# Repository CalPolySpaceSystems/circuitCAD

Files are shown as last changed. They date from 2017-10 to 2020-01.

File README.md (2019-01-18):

# Circuit CAD
This repository contains Cal Poly Space Systems' circuit board Design files. 
This includes designed PCBs as well as other resources.
See READMEs in each directory for more information.

# Projects
* UpBoard
* CubeStack
* Flight Recorders
* Peripherals
* Breakouts

# Resources
* Component Libraries
* Design Block/Subassembly Libraries
* CAM jobs for exporting Gerber Files of PCBs

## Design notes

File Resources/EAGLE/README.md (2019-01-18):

# EAGLE Resources
This collection currently contains:
* Parts Libraries
* Design Blocks 
* CAM Jobs
<p>
See each directory's README for more information.

# How to Use These Resources
In order to seamlessly import these resources into your EAGLE environment, follow these steps.

1. Clone this repository to your machine 
2. Open EAGLE. Go to the EAGLE control panel.
3. On the toolbar, select `options->directories`. This controls which directories EAGLE will look for files in. 
4. Add the locations of additional dependencies by placing a semicolon after the default directory followed by the local directory of the dependency.<p>
  
<b>Windows:</b><p>
<a href="https://imgur.com/tBfDsb9">Directory Examples</a>

5. Do this for all resource folders you wish to have access to in EAGLE.
6. Restart EAGLE.

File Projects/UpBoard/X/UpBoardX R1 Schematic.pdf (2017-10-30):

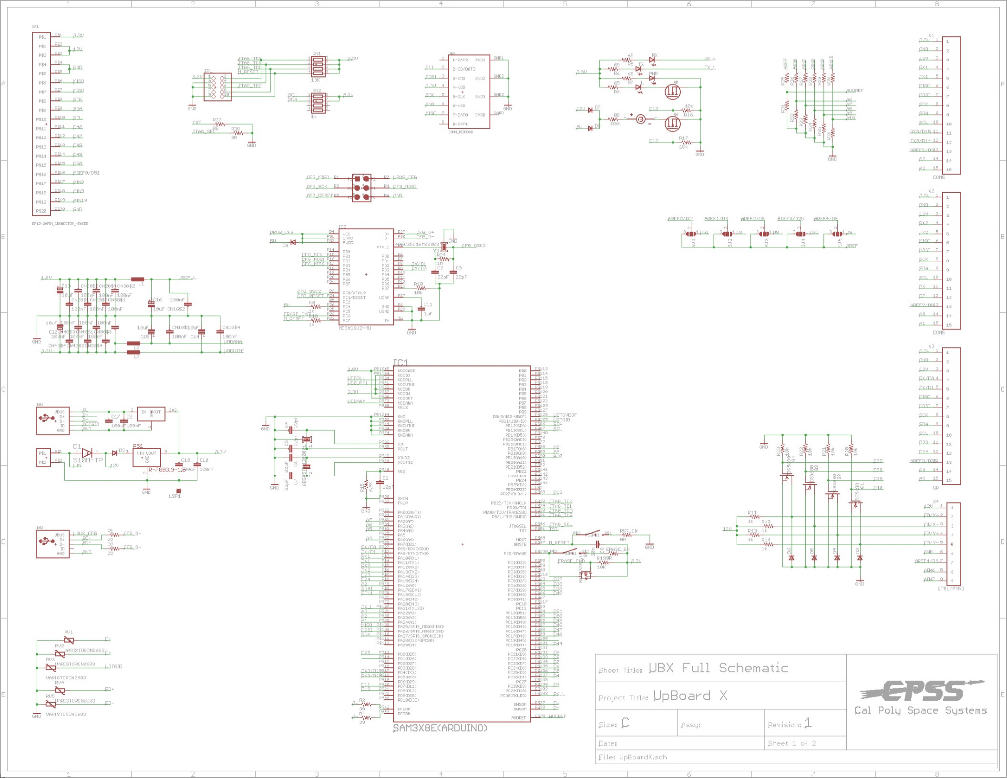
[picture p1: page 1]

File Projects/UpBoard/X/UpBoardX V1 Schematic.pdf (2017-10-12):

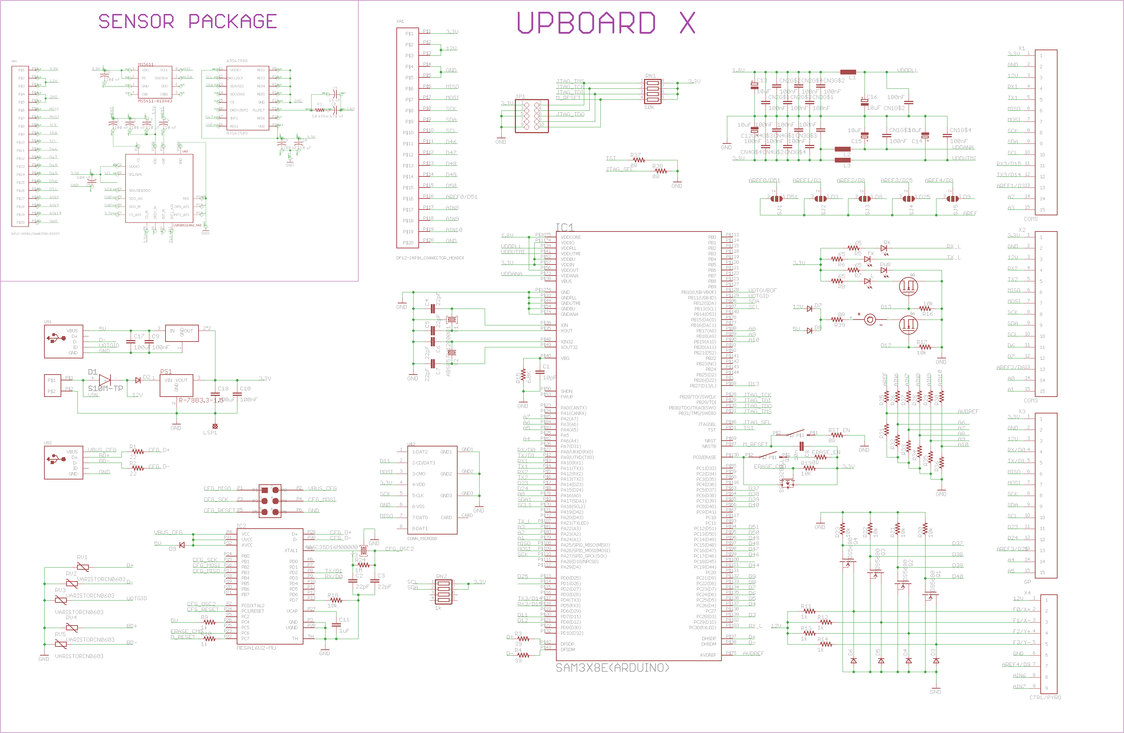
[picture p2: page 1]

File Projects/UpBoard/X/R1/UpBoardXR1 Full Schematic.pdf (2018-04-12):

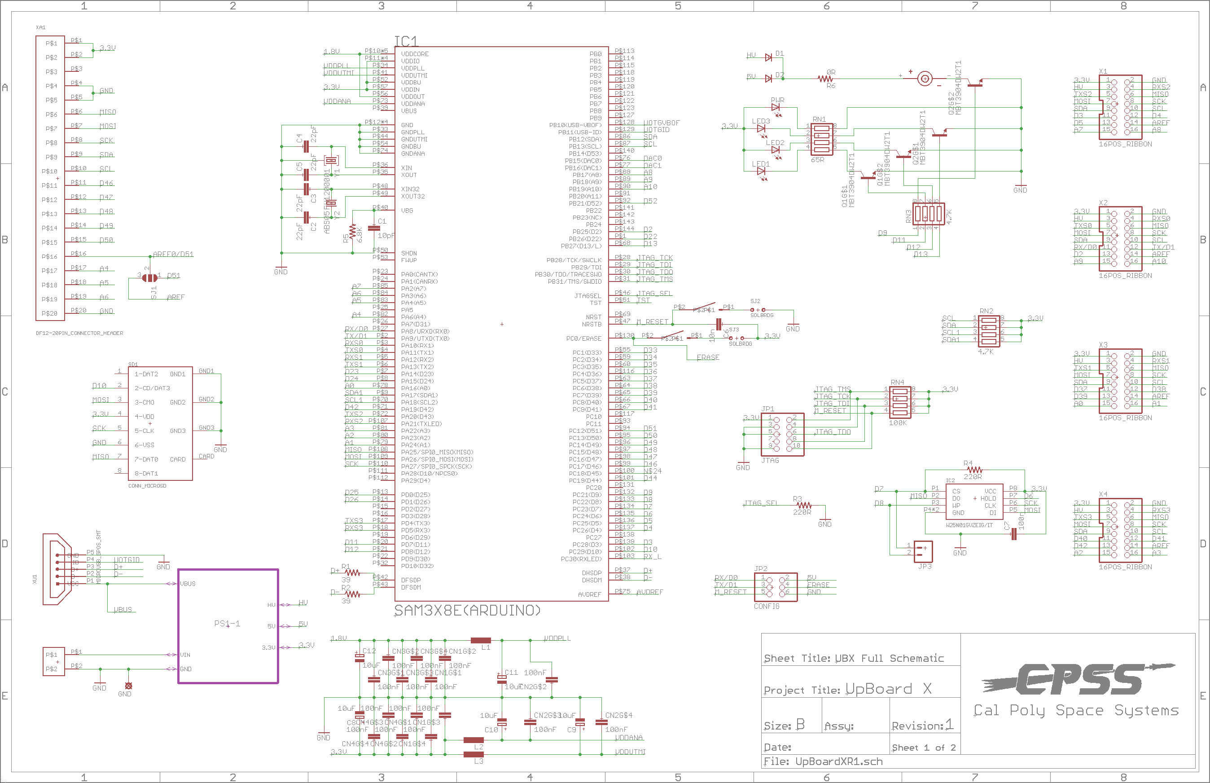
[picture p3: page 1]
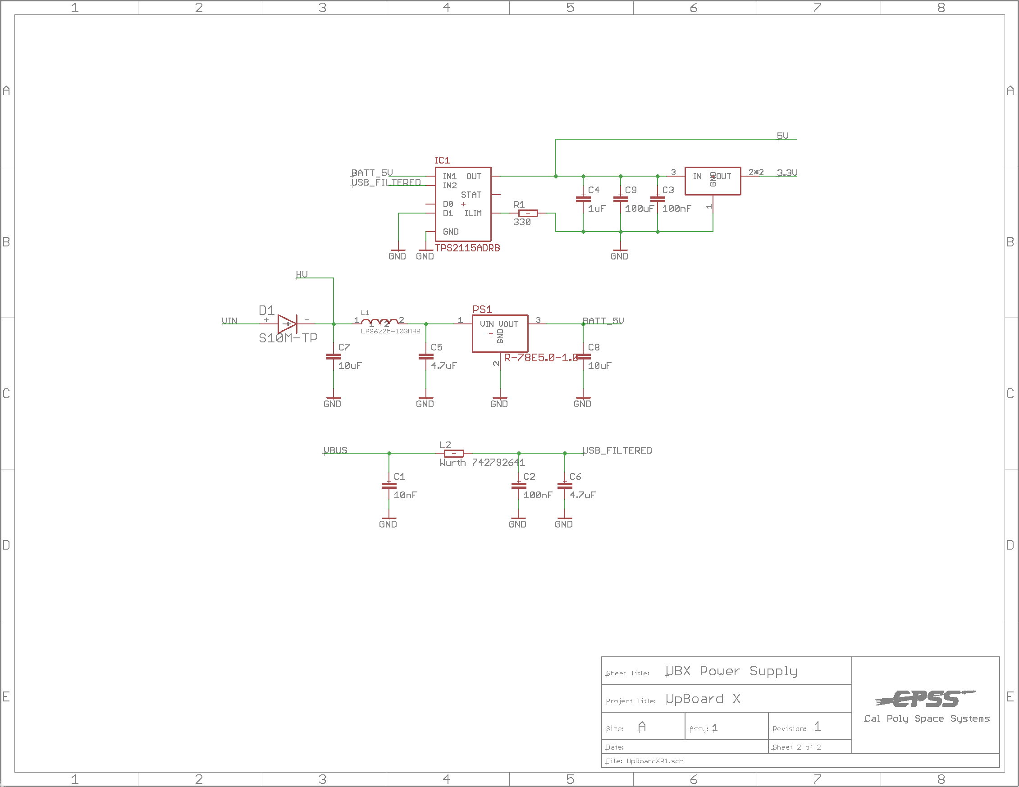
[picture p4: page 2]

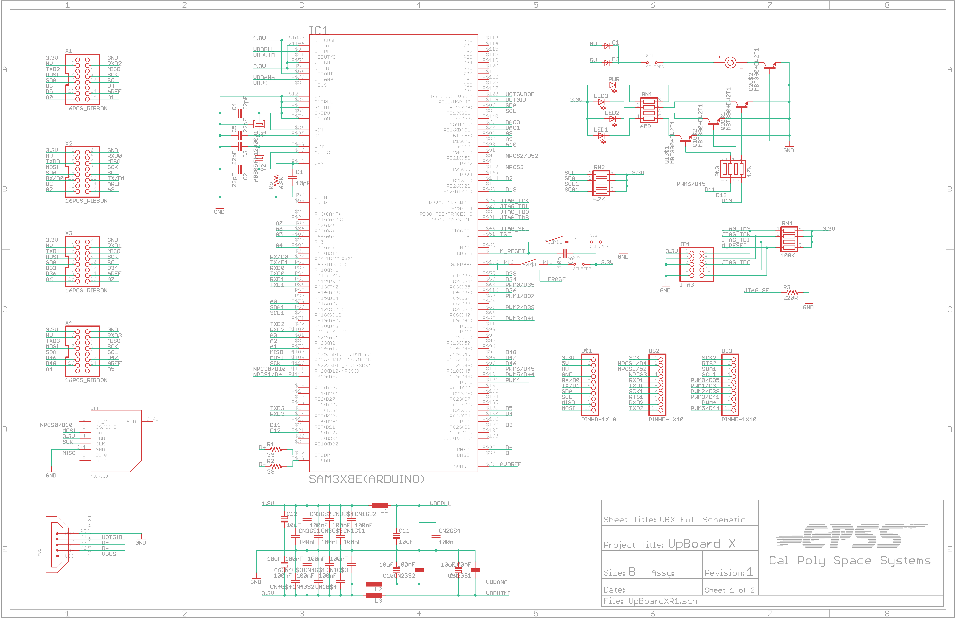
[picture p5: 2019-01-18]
Projects/CubeStack/SAM3X8E Core/cubestack core 1.png

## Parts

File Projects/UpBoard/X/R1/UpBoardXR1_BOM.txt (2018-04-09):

Partlist

Exported from UpBoardXR1.brd at 3/3/2018 10:47 AM

EAGLE Version 8.5.1 Copyright (c) 1988-2017 Autodesk, Inc.

Assembly variant: 

Part      Value                       Package            Library             Position (mil)        Orientation

C1        10pF                        C0603              resistor            (483.62205 1840.47244) R180
C2        22pF                        C0603              resistor            (547.24409 2049.6063) R180
C3        22pF                        C0603              resistor            (547.24409 2246.45669) R180
C4        22pF                        C0603              resistor            (543.54331 2346.37795) R0
C5        22pF                        C0603              resistor            (542.83465 2571.5748) R180
C6        10n                         C0603              resistor            (2356.37795 936.77165) R270
C7        100n                        C0603              resistor            (1800 1990)           R0
C8        10uF                        A/3216-18R         resistor            (1846.45669 1297.24409) R180
C9        10uF                        A/3216-18R         resistor            (1846.45669 1218.50394) R180
C10       10uF                        A/3216-18R         resistor            (1846.45669 1139.76378) R180
C11       10uF                        A/3216-18R         resistor            (1846.45669 1061.02362) R180
C12       10uF                        A/3216-18R         resistor            (1846.45669 982.28346) R180
CN1       100nF                       1206-4             resistor            (1652.75591 1295.27559) R270
CN2       100nF                       1206-4             resistor            (1652.75591 1137.79528) R90
CN3       100nF                       1206-4             resistor            (1652.75591 980.31496) R270
CN4       100nF                       1206-4             resistor            (1497.79528 1134.72441) R180
D1                                    SOD323             zetex               (2932.28346 1692.12598) R0
D2                                    SOD323             zetex               (2931.88976 1841.73228) R0
ERASE     1000P                       B3U-1000P          switch-omron        (2769.84252 1551.33858) R0
GND       LSP10                       LSP10              solpad              (913.30709 1375.11811) R180
IC1       SAM3X8E(ARDUINO)            144-LEAD_LQFP      ATSAM3X             (1100 2031.88976)     R270
IC2       W25N01GVZEIG/IT             WSON               CPSS_IC             (1993.54331 1792.3622) R90
JP1       JTAG                        2X05               pinhead             (2256.61417 2290.55118) R90
JP2       CONFIG                      2X03               pinhead             (2256.61417 1832.28346) R90
JP3                                   1X02               SparkFun-Connectors (1690 1800)           R0
L1                                    C0402              resistor            (1498.89764 1022.83465) R0
L2                                    C0402              resistor            (1496.37795 1262.99213) R0
L3                                    C0402              resistor            (1495.98425 1325.98425) R0
LED1                                  CHIPLED_0805       led                 (1960.62992 2119.68504) R90
LED2                                  CHIPLED_0805       led                 (1963.77953 2253.14961) R90
LED3                                  CHIPLED_0805       led                 (1964.56693 2385.03937) R90
LS1       AI-1440-TWT-24V-2-R         AI-1440-TWT-24-2-R UpBoard             (2718.11024 2124.40945) R180
PS1-1:C1  10nF                        C0603              eagle-ltspice       (1330 1180)           R0
PS1-1:C2  100nF                       C0603              eagle-ltspice       (710 1190)            R90
PS1-1:C3  100nF                       C0603              resistor            (903.77953 1204.96063) R90
PS1-1:C4  1uF                         C0805              eagle-ltspice       (990 1220)            R90
PS1-1:C5  4.7uF                       C1206              eagle-ltspice       (500 1150)            R0
PS1-1:C6  4.7uF                       C0805              eagle-ltspice       (820 1220)            R90
PS1-1:C7  10uF                        C1206              eagle-ltspice       (1277.48031 887.08661) R0
PS1-1:C8  10uF                        C1206              eagle-ltspice       (550 1290)            R0
PS1-1:C9  100uF                       C0805              resistor            (1080 1220)           R90
PS1-1:D1  S10M-TP                     DO-214AB           Power_Utils_Brett   (1274.72441 613.77953) R90
PS1-1:IC1 TPS2115ADRB                 SON-8              Power_Utils_Brett   (933.07087 994.01575) R270
PS1-1:L1  LPS6225-103MRB              INDM600X600X240N   Power_Utils_Brett   (1003.14961 750.31496) R180
PS1-1:L2  Wurth 742792641             R0603              eagle-ltspice       (1190 1180)           R180
PS1-1:PS1 R-78E5.0-1.0                R-78E5.0-1.0       Power_Utils_Brett   (719.68504 829.92126) R90
PS1-1:PS2 AZ1117C                     SOT89              UpBoard B           (1250.23622 1032.51969) R270
PS1-1:R1  330                         R0603              eagle-ltspice       (1015.98425 1090.55118) R0
PWR                                   CHIPLED_0805       led                 (1252.12598 1309.37008) R270
Q1        FFB2222A                    SC-88              CPSS_IC             (1645 2285)           R270
Q2        FFB2222A                    SC-88              CPSS_IC             (1745 2160)           R180
R1        39                          R0603              resistor            (1430 330)            R90
R2        39                          R0603              resistor            (1170 300)            R90
R3        220R                        R0402              resistor            (544.25197 1921.10236) R180
R4        220R                        R0402              resistor            (1710 1920)           R0
R5        6.8K                        R0603              resistor            (551.49606 1748.97638) R0
R6        0R                          R0603              resistor            (2564.96063 1803.93701) R0
RESET     1000P                       B3U-1000P          switch-omron        (2555.43307 1548.8189) R0
RN1       65R                         CTS742C083         resistor-net        (1805 2310)           R90
RN2       4.7K                        CTS742C083         resistor-net        (2056.14173 937.55906) R0
RN3       4.7K                        CTS742C083         resistor-net        (1680 2425)           R270
RN4       100K                        CTS742C083         resistor-net        (2207.95276 937.55906) R0
SD1       CONN_MICROSD                CONN_MICROSD       UpBoard B           (2430.04724 644.93701) R180
SJ1                                   SJ_2               jumper              (2037.40157 1180.31496) R270
SJ2       SOLBRDG                     SOLBRDG            CPSS_CONNECTOR      (2660 1470)           R270
SJ3       SOLBRDG                     SOLBRDG            CPSS_CONNECTOR      (2880 1470)           R270
X1        16POS_RIBBON                2X08               CPSS_CONNECTOR      (3300 890)            R270
X2        16POS_RIBBON                2X08               CPSS_CONNECTOR      (3303.14961 2110)     R270
X3        16POS_RIBBON                2X08               CPSS_CONNECTOR      (200 2110)            R90
X4        16POS_RIBBON                2X08               CPSS_CONNECTOR      (200 890)             R90
XA1       DF12-20PIN_CONNECTOR_HEADER DF12-HEADER        IMUPACKAGE          (2918.11024 1389.37008) R180
XP1       2POSTERMINALBLOCK.25"PITCH  OSTYK22102030      terminal_block      (676.37795 407.87402) R180
XU1       MICROUSB_5POS_SMT           RECPT_SMT_R/A      CPSS_CONNECTOR      (1300 80)             R0
Y1        FH1200001                   MINISMD            crystal             (543.54331 2449.13386) R90
Y2        ABS05                       FC-12M             crystal             (541.33858 2148.4252) R270

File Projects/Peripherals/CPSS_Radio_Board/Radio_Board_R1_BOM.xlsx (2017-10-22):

Part | list exported | from D:/Documents/eagle/CPSS | _Radio_Board/ | Radio_Board_R1.sch | at 10/22/2017 8:39 AM
Qty | Value | Device | Package | Parts | Description | Digikey | Mouser
1 |  | LED_E | LED_1206 | LED1 | LED | 404-1046-1-ND
2 | .1uF | C-USC0805 | C0805 | C8, C9 | CAPACITOR, American symbol | 399-1170-1-ND
1 | 0.01uF | C | C0805 | C2 | CAPACITOR, European symbol | 399-1158-1-ND
1 | 0.1uF | C | C0805 | C3 | CAPACITOR, European symbol | 399-1170-1-ND
3 | 0.1uF | C-USC0805 | C0805 | C15, C16, C17 | CAPACITOR, American symbol | 399-1170-1-ND
1 | 1.5k | R-US_M0805 | M0805 | R7 | RESISTOR, American symbol | 311-1.50KCRCT-ND
1 | 10 | R-US_R0805 | R0805 | R1 | RESISTOR, American symbol | 311-10.0CRCT-ND
2 | 10k | R-US_R0805 | R0805 | R2, R3 | RESISTOR, American symbol | 311-10KARCT-ND
1 | 10nF | C-USC0805 | C0805 | C1 | CAPACITOR, American symbol | 399-1158-1-ND
2 | 10uF | C-USC0805 | C0805 | C7, C10 | CAPACITOR, American symbol | 478-8115-1-ND
5 | 10uF | C-USC1206 | C1206 | C4, C19, C20, C21, |  | 478-8151-1-ND
1 | 15POSD-SUB | 15POSD-SUB | 15POSD-SUB | U$3 |  | A35118-ND
1 | 1uF | C-USC0805 | C0805 | C6 | CAPACITOR, American symbol | 490-1691-1-ND
2 | 27 | R-US_R0805 | R0805 | R5, R6 | RESISTOR, American symbol | 311-27.0CRCT-ND
1 | 27nH | R-US_R0805 | R0805 | L1 | RESISTOR, American symbol | 490-16032-1-ND
2 | 27pF | C-USC0603 | C0603 | C11, C12 | CAPACITOR, American symbol | 709-1173-1-ND
1 | 33nF | C-USC0805 | C0805 | C14 | CAPACITOR, American symbol | 445-6950-1-ND
1 | 4.7uF | C-USC1206 | C1206 | C18 | CAPACITOR, American symbol | 478-8265-1-ND
1 | 400 | R-US_R0805 | R0805 | R11 | RESISTOR, American symbol | 311-402CRCT-ND
1 | 470 | R-US_R0805 | R0805 | R4 | RESISTOR, American symbol | 311-470CRCT-ND
1 | 47pF | C-USC0805 | C0805 | C5 | CAPACITOR, American symbol | 490-3612-1-ND
1 | 60 | R-US_R0805 | R0805 | R8 | RESISTOR, American symbol | 311-59.0CRCT-ND
1 | ABBM-6 | ABBM-6 | SMD-4_NOLEAD | U$8 |  | 535-10156-1-ND
1 | BCW81SMD | BCW81SMD | SOT23-BEC | T1 | NPN Transistor | MMBT2222ALT1GOSCT-ND
2 | BLM15HG102SN1 | BLM15HG102SN1 | 402 | L2, L3 | EMIFIL (R) Chip Ferrite Bead for GHz Noise | 490-4003-1-ND
1 | BU-SMA-V | BU-SMA-V | BU-SMA-V | X1 | FEMALE SMA CONNECTOR
1 | FT2232D | FT2232D | QFP48-7X7 | IC1 | FT2232 DUAL USB UART/FIFO (4th Gen USB 2 full speed) | 768-1010-1-ND
1 | LT1963A-3.3 | LT1963A-3.3 | SOT223 | U$7 |  | LT1963AEST-3.3#TRPBFCT-ND
1 | MC74VHC1G125 | MC74VHC1G125 | SC70-5L | U$6 |  |  | 863-M74VHC1G125DFT1G
1 | MINI-USB-UX60 | -MB-5S8 MINI-USB-UX60-MB-5S8 | UX60-MB-5S8 | X2 | MINI USB Connector | H2960CT-ND
1 | NEO-M8 | NEO-M8 | NEO-M8 | U$1 | u-blox NEO GNSS module | 672-1008-1-ND
1 | R-78E5.0-1.0 | R-78E5.0-1.0 | R-78E5.0-1.0 | U$5 |  | 945-2201-ND
1 | TPS2115A | TPS2115A | TSSOP-8 | U$4 |  |  | 595-TPS2115APWR
1 | XBEE-PRO_900H | P XBEE-PRO_900HP | XBEE_S3B | U$2 |  | 602-1299-ND

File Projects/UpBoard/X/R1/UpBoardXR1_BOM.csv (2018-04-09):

Partlist
Exported from UpBoardXR1.sch at 3/3/2018 10:50 AM
EAGLE Version 8.5.1 Copyright (c) 1988-2017 Autodesk, Inc.
Assembly variant:
Part      Value                       Device                      Package            Library             Sheet
C1        10pF                        C-EUC0603                   C0603              resistor            1
C2        22pF                        C-EUC0603                   C0603              resistor            1
C3        22pF                        C-EUC0603                   C0603              resistor            1
C4        22pF                        C-EUC0603                   C0603              resistor            1
C5        22pF                        C-EUC0603                   C0603              resistor            1
C6        10n                         C-EUC0603                   C0603              resistor            1
C7        100n                        C-EUC0603                   C0603              resistor            1
C8        10uF                        CPOL-EUA/3216-18R           A/3216-18R         resistor            1
C9        10uF                        CPOL-EUA/3216-18R           A/3216-18R         resistor            1
C10       10uF                        CPOL-EUA/3216-18R           A/3216-18R         resistor            1
C11       10uF                        CPOL-EUA/3216-18R           A/3216-18R         resistor            1
C12       10uF                        CPOL-EUA/3216-18R           A/3216-18R         resistor            1
CN1       100nF                       CNET                        1206-4             resistor            1
CN2       100nF                       CNET                        1206-4             resistor            1
CN3       100nF                       CNET                        1206-4             resistor            1
CN4       100nF                       CNET                        1206-4             resistor            1
D1                                    DSOD323                     SOD323             zetex               1
D2                                    DSOD323                     SOD323             zetex               1
ERASE     1000P                       1000P                       B3U-1000P          switch-omron        1
GND       LSP10                       LSP10                       LSP10              solpad              1
IC1       SAM3X8E(ARDUINO)            SAM3X8E(ARDUINO)            144-LEAD_LQFP      ATSAM3X             1
IC2       W25N01GVZEIG/IT             W25N01GVZEIG/IT             WSON               CPSS_IC             1
JP1       JTAG                        PINHD-2X5                   2X05               pinhead             1
JP2       CONFIG                      PINHD-2X3                   2X03               pinhead             1
JP3                                   CONN_02                     1X02               SparkFun-Connectors 1
L1                                    L-EU0402                    C0402              resistor            1
L2                                    L-EU0402                    C0402              resistor            1
L3                                    L-EU0402                    C0402              resistor            1
LED1                                  LEDCHIPLED_0805             CHIPLED_0805       led                 1
LED2                                  LEDCHIPLED_0805             CHIPLED_0805       led                 1
LED3                                  LEDCHIPLED_0805             CHIPLED_0805       led                 1
LS1       AI-1440-TWT-24V-2-R         AI-1440-TWT-24V-2-R         AI-1440-TWT-24-2-R UpBoard             1
PS1-1:C1  10nF                        CC0603                      C0603              eagle-ltspice       PS1:1
PS1-1:C2  100nF                       CC0603                      C0603              eagle-ltspice       PS1:1
PS1-1:C3  100nF                       C-EUC0603                   C0603              resistor            PS1:1
PS1-1:C4  1uF                         C                           C0805              eagle-ltspice       PS1:1
PS1-1:C5  4.7uF                       CC1206                      C1206              eagle-ltspice       PS1:1
PS1-1:C6  4.7uF                       C                           C0805              eagle-ltspice       PS1:1
PS1-1:C7  10uF                        CC1206                      C1206              eagle-ltspice       PS1:1
PS1-1:C8  10uF                        CC1206                      C1206              eagle-ltspice       PS1:1
PS1-1:C9  100uF                       C-EUC0805                   C0805              resistor            PS1:1
PS1-1:D1  S10M-TP                     S10M-TP                     DO-214AB           Power_Utils_Brett   PS1:1
PS1-1:IC1 TPS2115ADRB                 TPS2115ADRB                 SON-8              Power_Utils_Brett   PS1:1
PS1-1:L1  LPS6225-103MRB              LPS6225-154MRB              INDM600X600X240N   Power_Utils_Brett   PS1:1
PS1-1:L2  Wurth 742792641             RR0603                      R0603              eagle-ltspice       PS1:1
PS1-1:PS1 R-78E5.0-1.0                R-78E5.0-1.0                R-78E5.0-1.0       Power_Utils_Brett   PS1:1
PS1-1:PS2 AZ1117C                     AZ1117C                     SOT89              UpBoard B           PS1:1
PS1-1:R1  330                         RR0603                      R0603              eagle-ltspice       PS1:1
PWR                                   LEDCHIPLED_0805             CHIPLED_0805       led                 1
Q1        FFB2222A                    FFB2222A                    SC-88              CPSS_IC             1
Q2        FFB2222A                    FFB2222A                    SC-88              CPSS_IC             1
R1        39                          R-US_R0603                  R0603              resistor            1
R2        39                          R-US_R0603                  R0603              resistor            1
R3        220R                        R-US_R0402                  R0402              resistor            1
R4        220R                        R-US_R0402                  R0402              resistor            1
R5        6.8K                        R-US_R0603                  R0603              resistor            1
R6        0R                          R-US_R0603                  R0603              resistor            1
RESET     1000P                       1000P                       B3U-1000P          switch-omron        1
RN1       65R                         CTS742C083                  CTS742C083         resistor-net        1
RN2       4.7K                        CTS742C083                  CTS742C083         resistor-net        1
RN3       4.7K                        CTS742C083                  CTS742C083         resistor-net        1
RN4       100K                        CTS742C083                  CTS742C083         resistor-net        1
SD1       CONN_MICROSD                CONN_MICROSD                CONN_MICROSD       UpBoard B           1
SJ1                                   SJ2W                        SJ_2               jumper              1
SJ2       SOLBRDG                     SOLBRDG                     SOLBRDG            CPSS_CONNECTOR      1
SJ3       SOLBRDG                     SOLBRDG                     SOLBRDG            CPSS_CONNECTOR      1
X1        16POS_RIBBON                16POS_RIBBON                2X08               CPSS_CONNECTOR      1
X2        16POS_RIBBON                16POS_RIBBON                2X08               CPSS_CONNECTOR      1
X3        16POS_RIBBON                16POS_RIBBON                2X08               CPSS_CONNECTOR      1
X4        16POS_RIBBON                16POS_RIBBON                2X08               CPSS_CONNECTOR      1
XA1       DF12-20PIN_CONNECTOR_HEADER DF12-20PIN_CONNECTOR_HEADER DF12-HEADER        IMUPACKAGE          1
XP1       2POSTERMINALBLOCK.25"PITCH  2POSTERMINALBLOCK.25"PITCH  OSTYK22102030      terminal_block      1
XU1       MICROUSB_5POS_SMT           MICROUSB_5POS_SMT           RECPT_SMT_R/A      CPSS_CONNECTOR      1
Y1        FH1200001                   FH1200001                   MINISMD            crystal             1
Y2        ABS05                       ABS05                       FC-12M             crystal             1

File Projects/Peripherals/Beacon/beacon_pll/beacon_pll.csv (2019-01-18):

Source: | C:\Users\BrianG\Documents\PCB\Beacon\beacon_pll\beacon_pll.sch
Date: | 8/25/2018 11:21:02 AM
Tool: | Eeschema (5.0.0-rc2-dev-311-g1dd4af297)
Generator: | C:\Program Files\KiCad\bin\scripting\plugins/bom_csv_grouped_by_value_with_fp.py
Component Count: | 52
Ref | Qnty | Value | Cmp name | Footprint | Description | Vendor
C1, | 1 | 10u | CP | Capacitors_SMD:C_1206_HandSoldering | Polarised capacitor
C2, | 1 | 50u | CP | Capacitors_Tantalum_SMD:CP_Tantalum_Case-R_EIA-2012-12_Hand | Polarised capacitor
C8, C7, | 2 | 10n | C | Capacitors_SMD:C_0805_HandSoldering | Unpolarized capacitor
C9, | 1 | 27n | C | Capacitors_SMD:C_0805_HandSoldering | Unpolarized capacitor
C11, | 1 | 10u | CP | Capacitors_SMD:C_0805_HandSoldering | Polarised capacitor
C12, C14, C16, C4, C3, | 5 | 0.1u | C | Capacitors_SMD:C_0805_HandSoldering | Unpolarized capacitor
C13, C15, C18, | 3 | 10p | C | Capacitors_SMD:C_0805_HandSoldering | Unpolarized capacitor
C19, C20, | 2 | 100p | C | Capacitors_SMD:C_0805_HandSoldering | Unpolarized capacitor
C21, | 1 | 560p | C | Capacitors_SMD:C_0805_HandSoldering | Unpolarized capacitor
C22, | 1 | 8.2n | C | Capacitors_SMD:C_0805_HandSoldering | Unpolarized capacitor
C23, | 1 | 1u | C | Capacitors_SMD:C_0805_HandSoldering | Unpolarized capacitor
C24, | 1 | 1n | C | Capacitors_SMD:C_0805_HandSoldering | Unpolarized capacitor
C25, | 1 | 150p | C | Capacitors_SMD:C_0805_HandSoldering | Unpolarized capacitor
C27, C17, C26, | 3 | 270p | C | Capacitors_SMD:C_0805_HandSoldering | Unpolarized capacitor
D1, | 1 | BYS10-45-E3/TR | D_Schottky | Diodes_SMD:D_SMA_Handsoldering | Schottky diode
D3, | 1 | LED | LED | LEDs:LED_0805_HandSoldering | LED generic
J1, | 1 | OUTPUT CONNECTOR | Conn_01x12 | Pin_Headers:Pin_Header_Straight_2x06_Pitch2.54mm | Generic connector, single row, 01x12, script generated (kicad-library-utils/schlib/autogen/connector/)
J4, | 1 | SMA OUT | Conn_Coaxial | Connectors_Amphenol:Amphenol_RF_SMA_132289 | coaxial connector (BNC, SMA, SMB, SMC, Cinch/RCA, ...)
L1, | 1 | MH2029-300Y | Ferrite_Bead | Inductors_SMD:L_0805_HandSoldering | Ferrite bead
L2, L4, | 2 | 55.0n | L | Inductors_SMD:L_0805_HandSoldering | Inductor
L3, L5, | 2 | 53n | L | Inductors_SMD:L_0805_HandSoldering | Inductor
L6, | 1 | 72n | L | Inductors_SMD:L_0805_HandSoldering | Inductor
R1, | 1 | 50k | R | Resistors_SMD:R_0805_HandSoldering | Resistor
R4, | 1 | 2.2k | R | Resistors_SMD:R_0805_HandSoldering | Resistor
R8, | 1 | 10k | R | Resistors_SMD:R_0805_HandSoldering | Resistor
R9, R7, | 2 | 0 | R | Resistors_SMD:R_0805_HandSoldering | Resistor
R10, | 1 | 4.7k | R | Resistors_SMD:R_0805_HandSoldering | Resistor
R11, | 1 | 1.3k | R | Resistors_SMD:R_0805_HandSoldering | Resistor
R13, R14, | 2 | 470 | R | Resistors_SMD:R_0805_HandSoldering | Resistor
R16, R15, | 2 | 50 | R | Resistors_SMD:R_0805_HandSoldering | Resistor
R17, | 1 | 13k | R | Resistors_SMD:R_0805_HandSoldering | Resistor
R18, | 1 | 27k | R | Resistors_SMD:R_0805_HandSoldering | Resistor
U1, | 1 | LM1117-3.3 | LM1117-3.3 | TO_SOT_Packages_SMD:SOT-223 | 800mA Low-Dropout Linear Regulator, 1.8V fixed output, TO-220/TO-252/TO-263/SOT-223
U2, | 1 | TXB0104D | TXB0104D | Housings_SOIC:SOIC-14_3.9x8.7mm_Pitch1.27mm | 4-Bit Bidirectional Voltage-Level Translator, Auto Direction Sensing and ±15-kV ESD Protection, 1.2 - 3.6 V APort, 1.65 - 5.5 V BPort, SOIC-14
U3, | 1 | ADF4360-8 | ADF4360-8 | Housings_CSP:ADF4360-8BCPZRL7
U4, | 1 | QPA4463ASR | QPA4463ASR | TO_SOT_Packages_SMD:SOT-363_SC-70-6_Handsoldering
X1, | 1 | ASEMB-10.000MHz | ASE-xxxMHz | Oscillators:Oscillator_SMD_Abracon_ASE-4pin_3.2x2.5mm | 3.3V CMOS SMD Crystal Clock Oscillator, Abracon

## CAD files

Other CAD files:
Projects/Peripherals/StrainGaugeBoard/Packages/QFN40P400X400X80-29N/qfn40p400x400x80-29n.psm

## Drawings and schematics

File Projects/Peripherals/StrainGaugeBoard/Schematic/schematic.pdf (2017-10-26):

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
## Strain Gauge Measurement Board

This board was designed to take readings from up-to 10 resistive bridge sensors at a time with high speed, high accuracy, and low noise. The ADC that handles the measurement is the MAX11410 from Maxim Integrated. This
is a 24-bit 5 channel differential sigma-delta ADC with sample rates of up to 1.9ksps. With this board requiring a minimum sample rate of 50sps, this ADC performs well enough with its multiplexed analog input.

1.9ksps / ( 2ADCs * 5channels ) = 190sps max

Accounting for worst case scenario time transient of the ADC's internals per read cycle across both ADCs:

240us * 2 + 2us * 2 + 2us * 10 ~= 0.5ms spent waiting for signals to settle resulting in a theoretical MAX sample rate of 170sps for the ADC's in the configuration of this board.

Title

Size Document Number | Rev
Date: | Sheet | of
| Created by:
01-001 | 1

STRAIN GAUGE BOARD - OVERVIEW

CAL POLY SPACE SYSTEMS (CPSS)

### 1 GRAND AVE., SAN LUIS OBISPO, CA 93407

A
Thursday, October 26, 2017 | 1 | 13
J. NGUYEN

Title

Size Document Number | Rev
Created by:
01-001 | 1

STRAIN GAUGE BOARD - OVERVIEW

CAL POLY SPACE SYSTEMS (CPSS)

### 1 GRAND AVE., SAN LUIS OBISPO, CA 93407

A
Thursday, October 26, 2017 | 1 | 13
J. NGUYEN

Title

Size Document Number | Rev
Created by:
01-001 | 1

STRAIN GAUGE BOARD - OVERVIEW

CAL POLY SPACE SYSTEMS (CPSS)

### 1 GRAND AVE., SAN LUIS OBISPO, CA 93407

A
Thursday, October 26, 2017 | 1 | 13
J. NGUYEN

AIN9 12 | AGND 13 | AVDD ¹⁴
CAPREG 22 | VDDIO ²³ GND 24

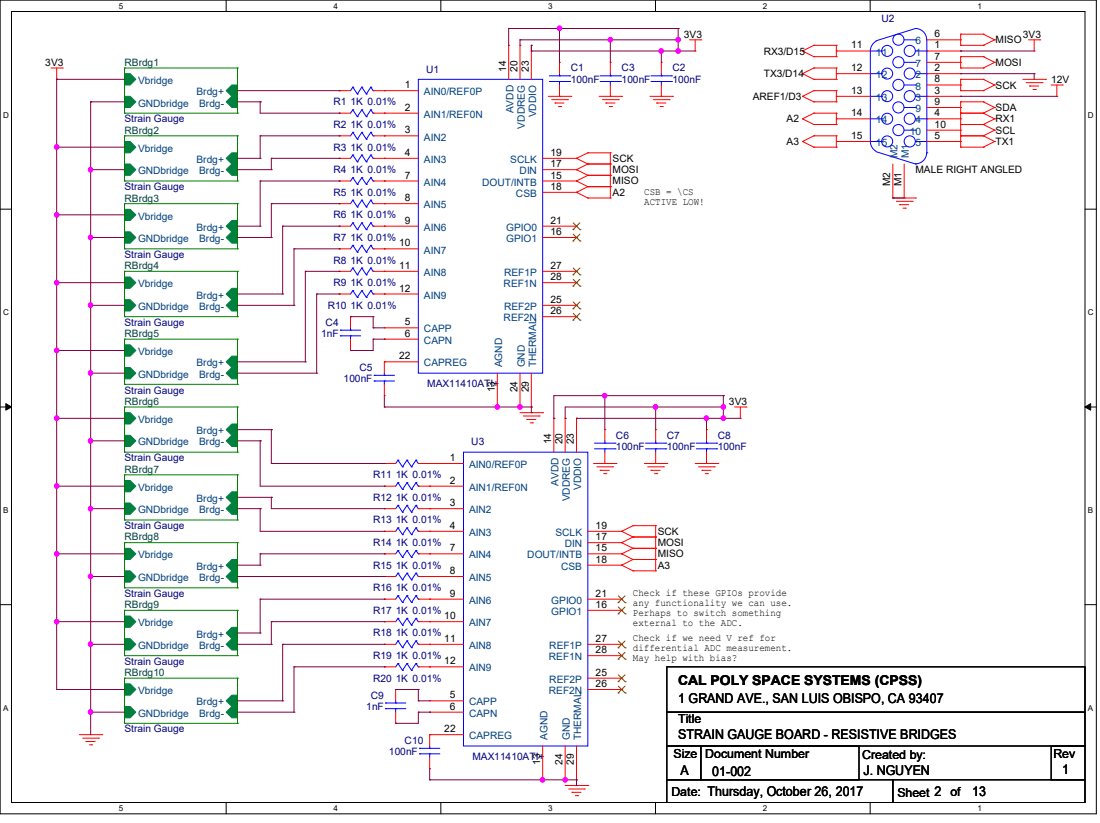
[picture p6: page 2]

Check if these GPIOs provide
any functionality we can use.
Perhaps to switch something
external to the ADC.
A Check if we need V ref for
differential ADC measurement.
May help with bias?
CAL POLY SPACE SYSTEMS (CPSS)
1 GRAND AVE., SAN LUIS OBISPO, CA 93407 A
Title
STRAIN GAUGE BOARD - RESISTIVE BRIDGES

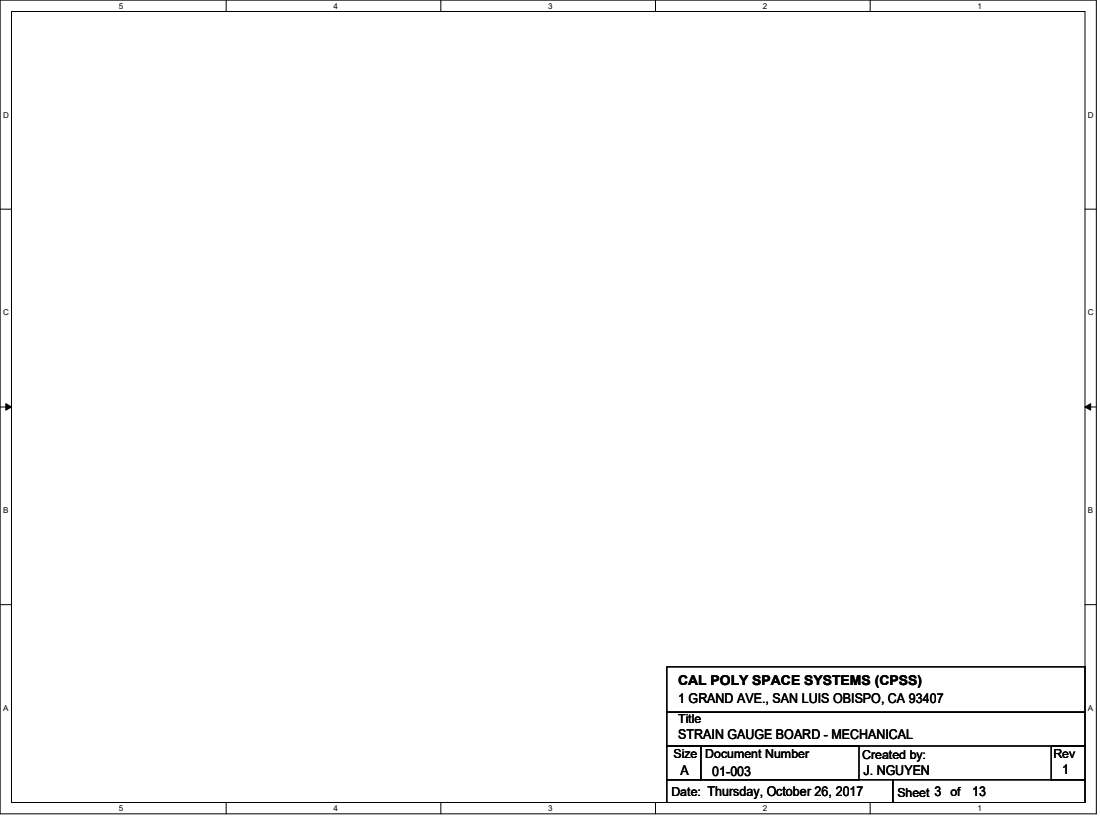
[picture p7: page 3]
Size Document Number; Rev; Created by:; Thursday, October 26, 2017; J. NGUYEN

CAL POLY SPACE SYSTEMS (CPSS)
1 GRAND AVE., SAN LUIS OBISPO, CA 93407
Title
STRAIN GAUGE BOARD - MECHANICAL

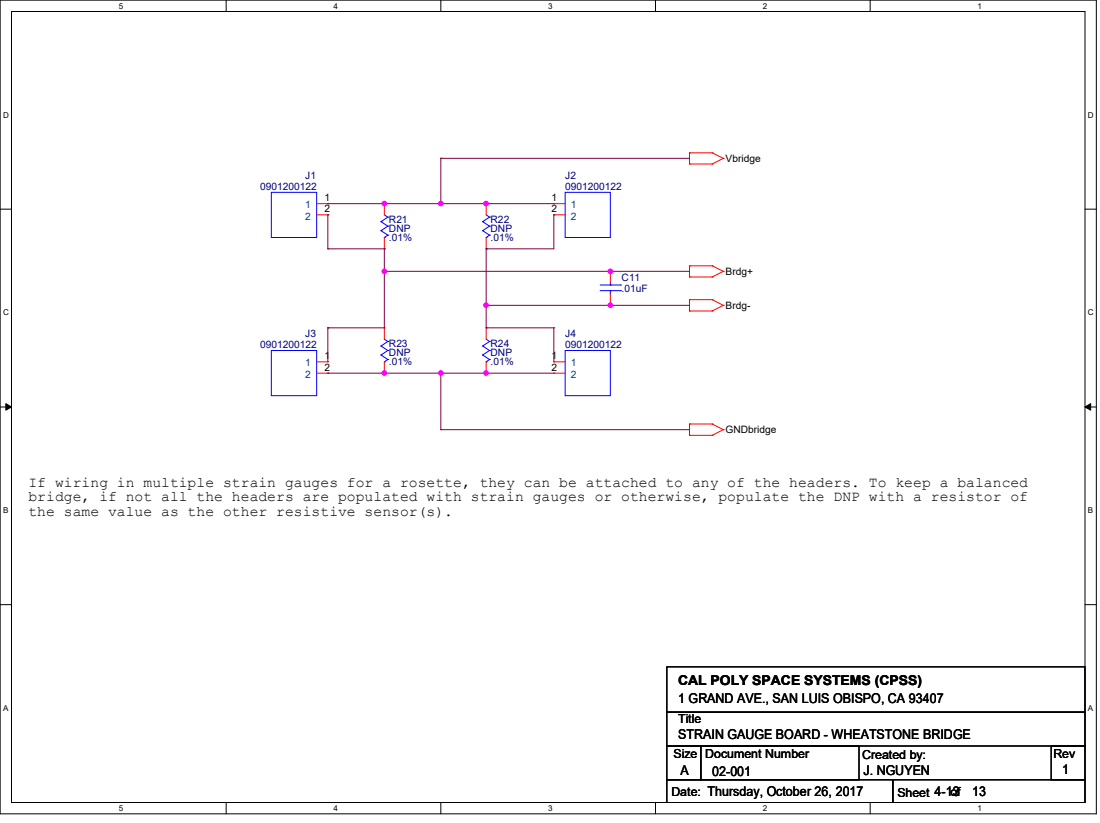
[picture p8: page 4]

If wiring in multiple strain gauges for a rosette, they can be attached to any of the headers. To keep a balanced
bridge, if not all the headers are populated with strain gauges or otherwise, populate the DNP with a resistor of
the same value as the other resistive sensor(s).

CAL POLY SPACE SYSTEMS (CPSS)
1 GRAND AVE., SAN LUIS OBISPO, CA 93407
Title
STRAIN GAUGE BOARD - WHEATSTONE BRIDGE

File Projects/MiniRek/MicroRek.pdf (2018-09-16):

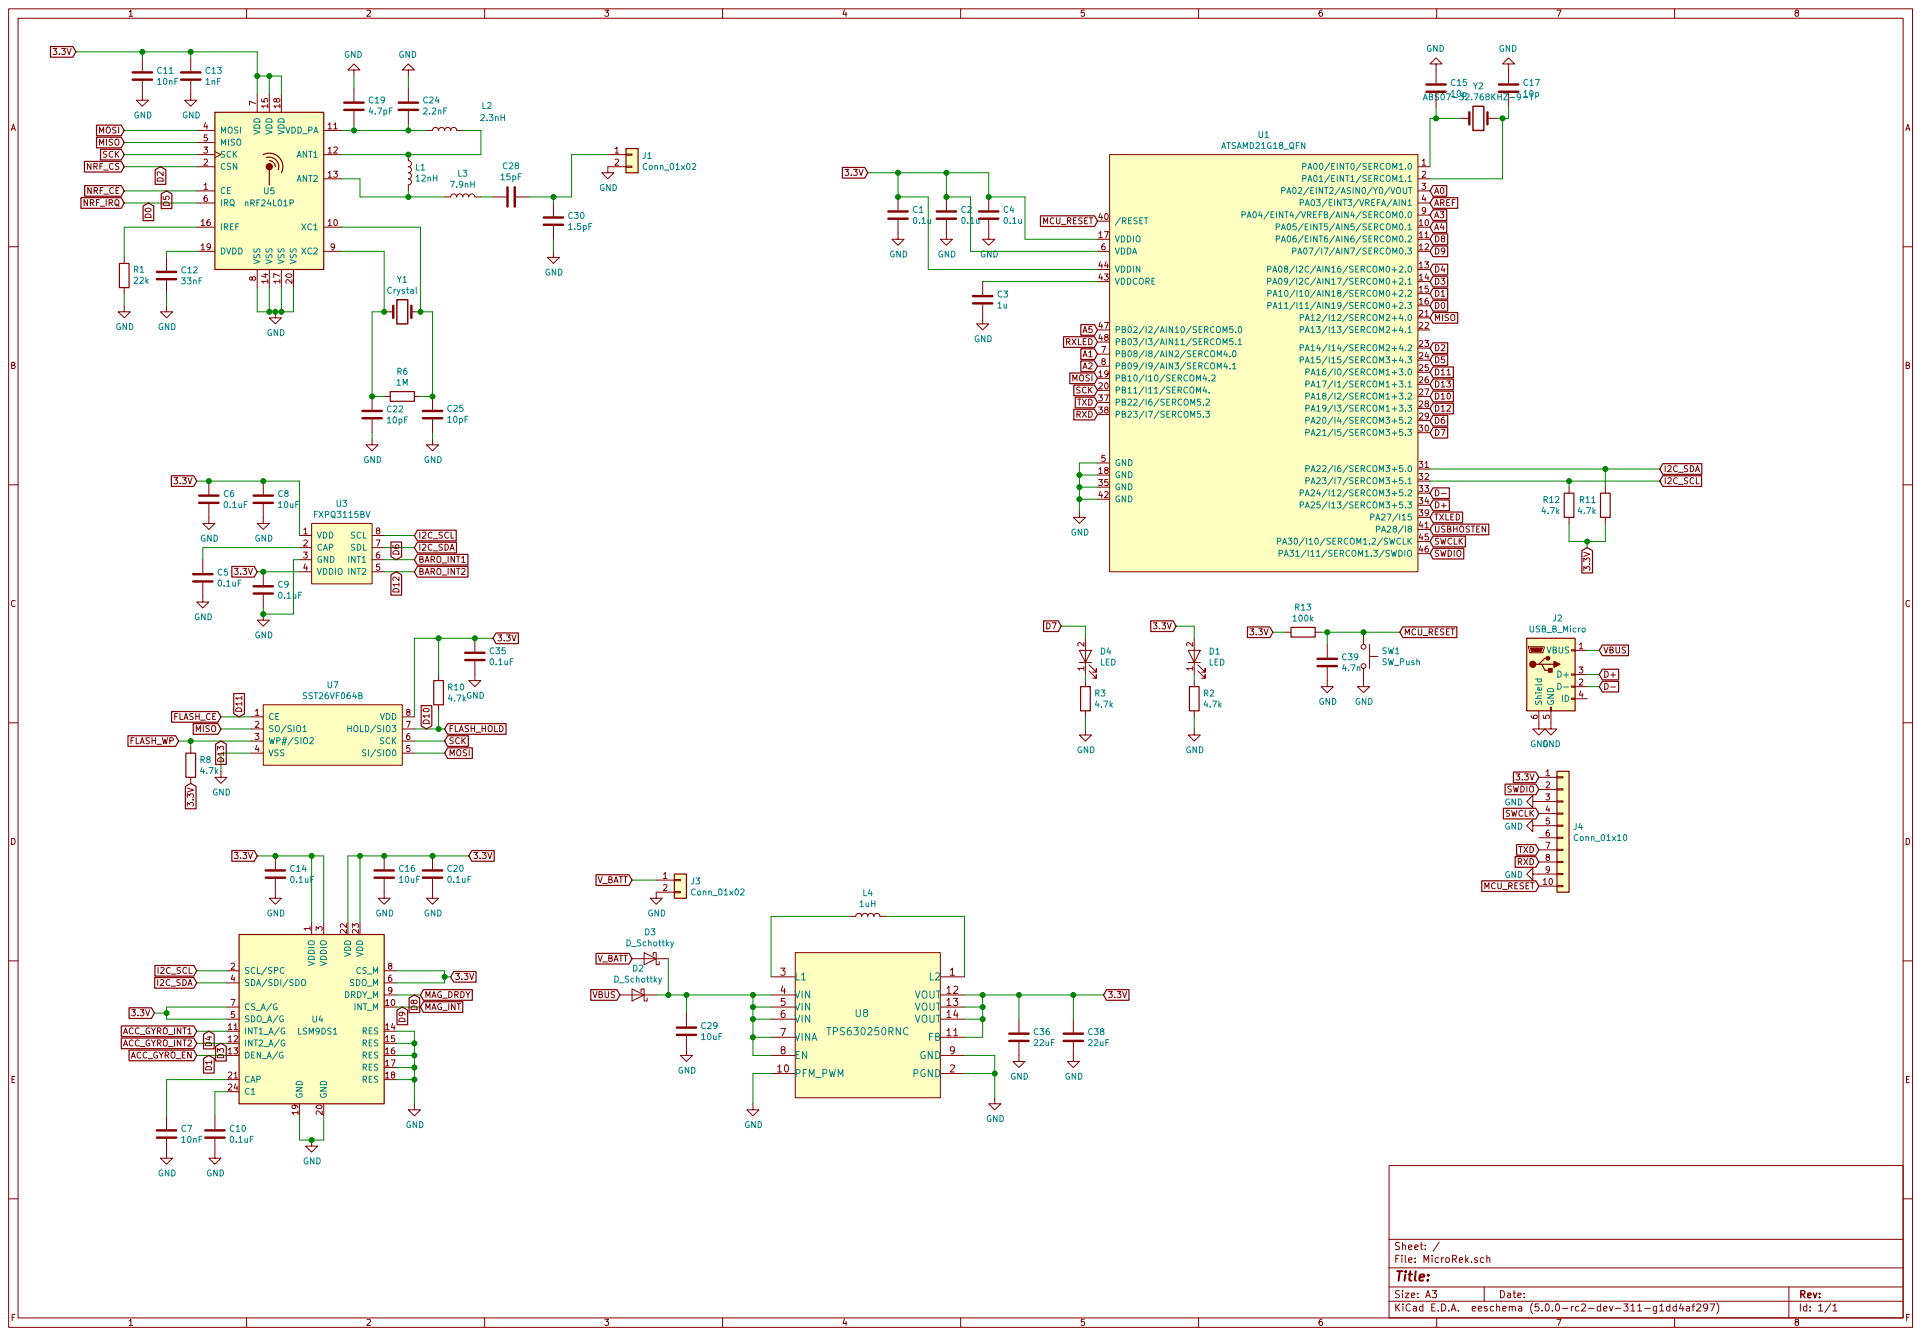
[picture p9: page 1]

SWDIO
SWCLK MCU_RESET GND GND GND

Id: 1/1 Title: File: MicroRek.sch Sheet: /

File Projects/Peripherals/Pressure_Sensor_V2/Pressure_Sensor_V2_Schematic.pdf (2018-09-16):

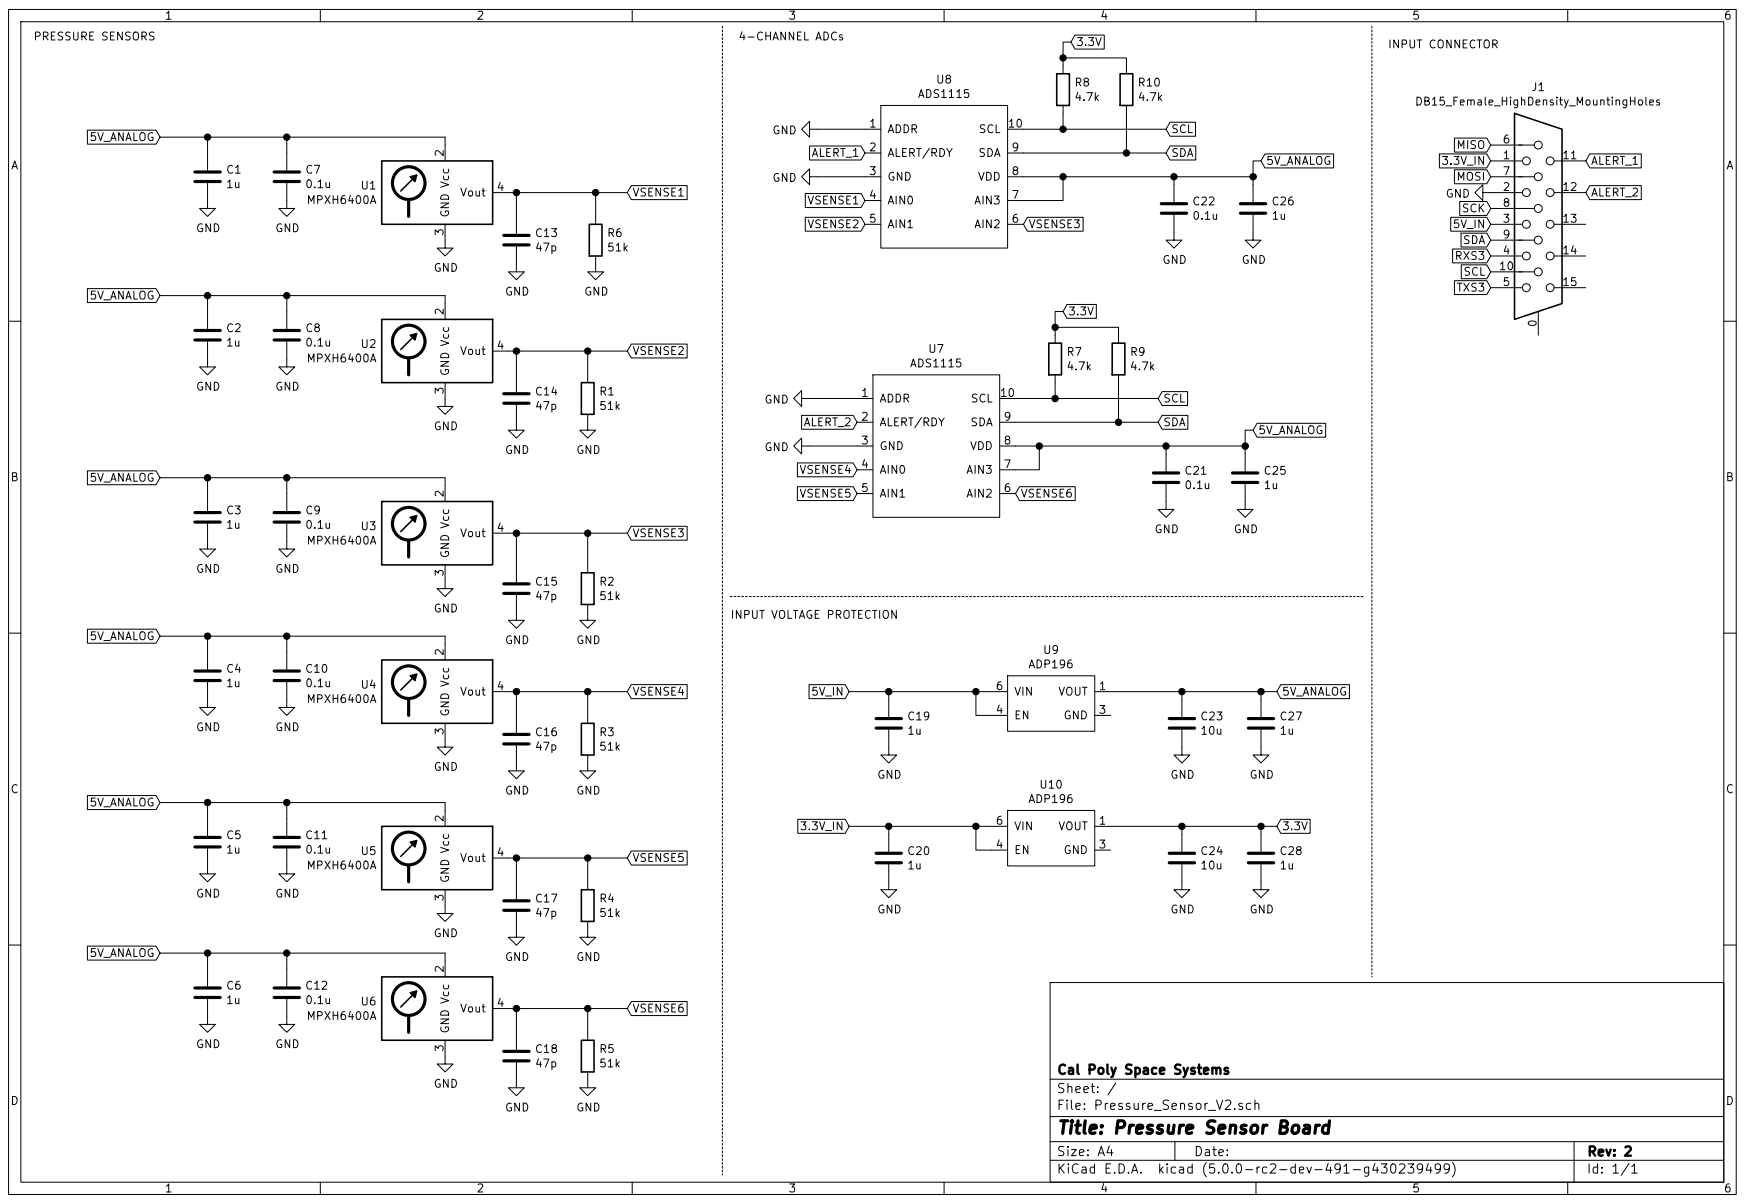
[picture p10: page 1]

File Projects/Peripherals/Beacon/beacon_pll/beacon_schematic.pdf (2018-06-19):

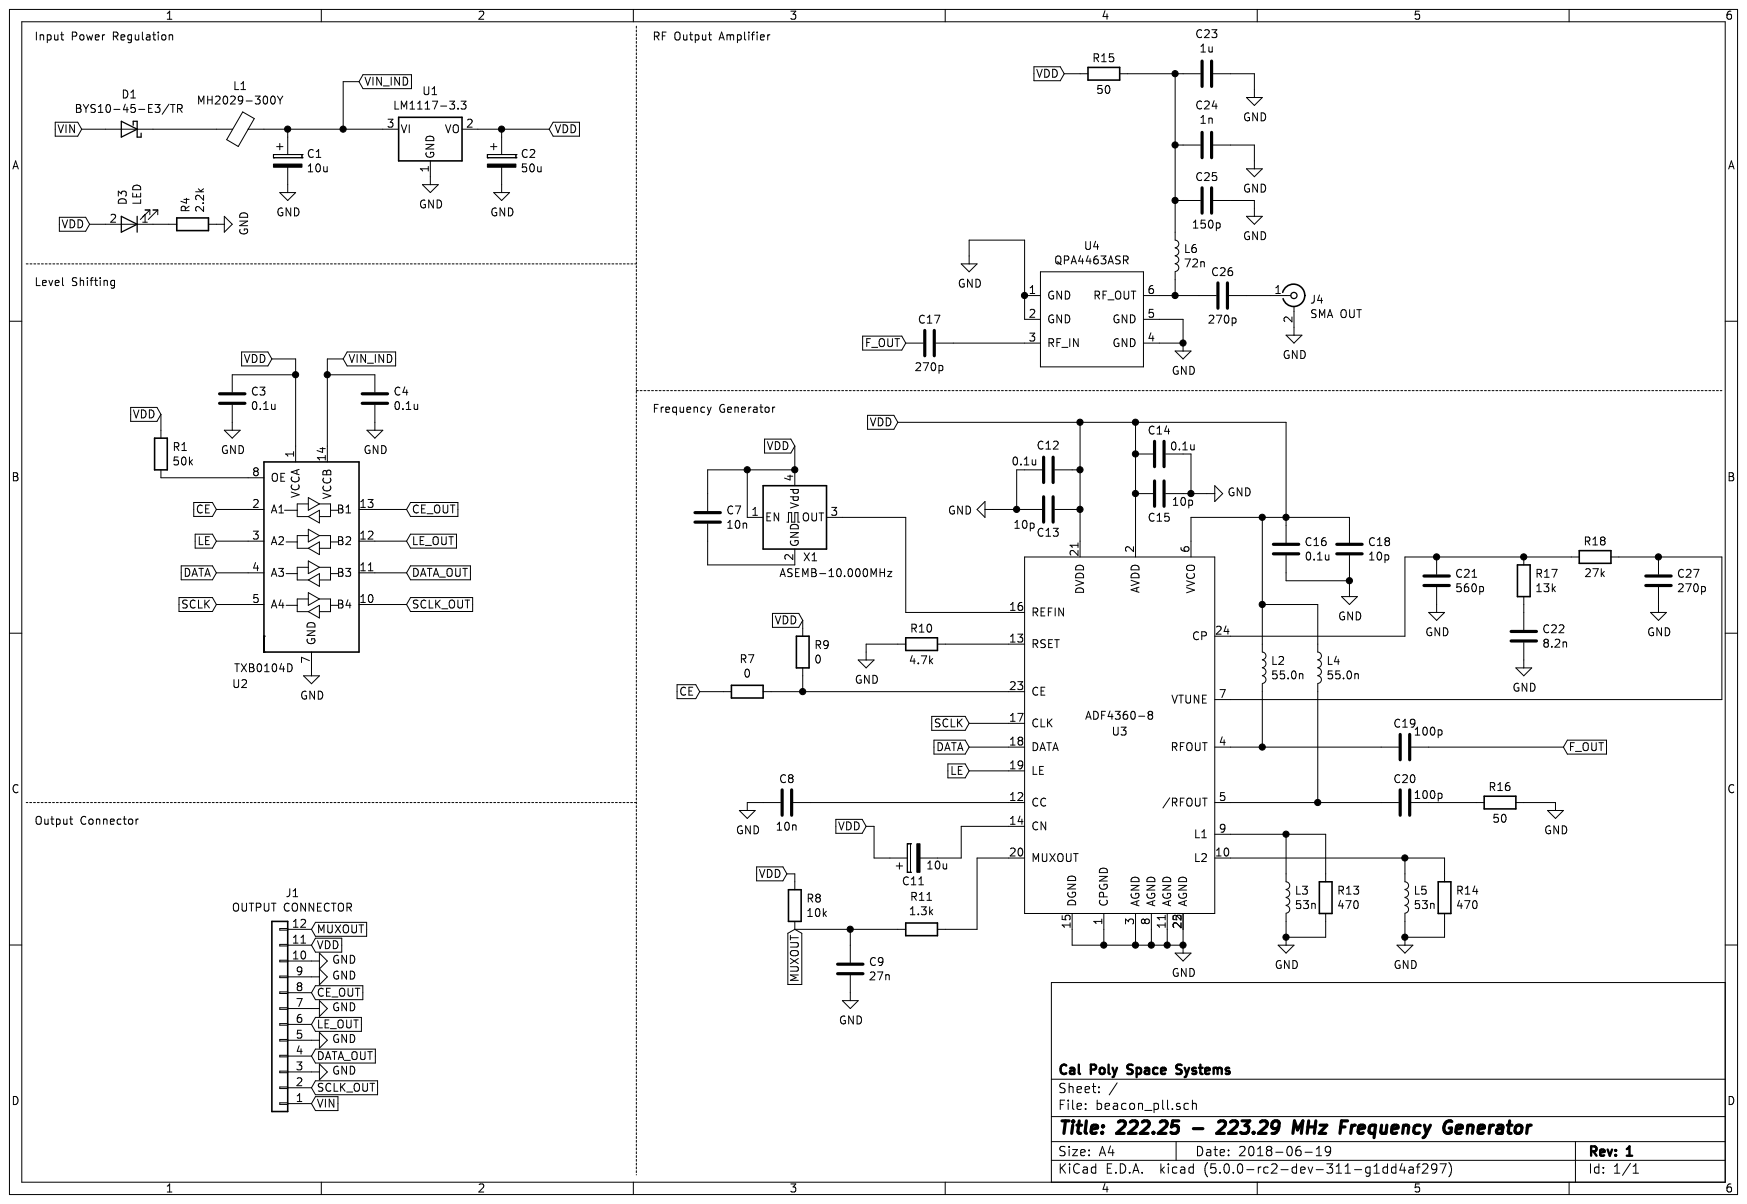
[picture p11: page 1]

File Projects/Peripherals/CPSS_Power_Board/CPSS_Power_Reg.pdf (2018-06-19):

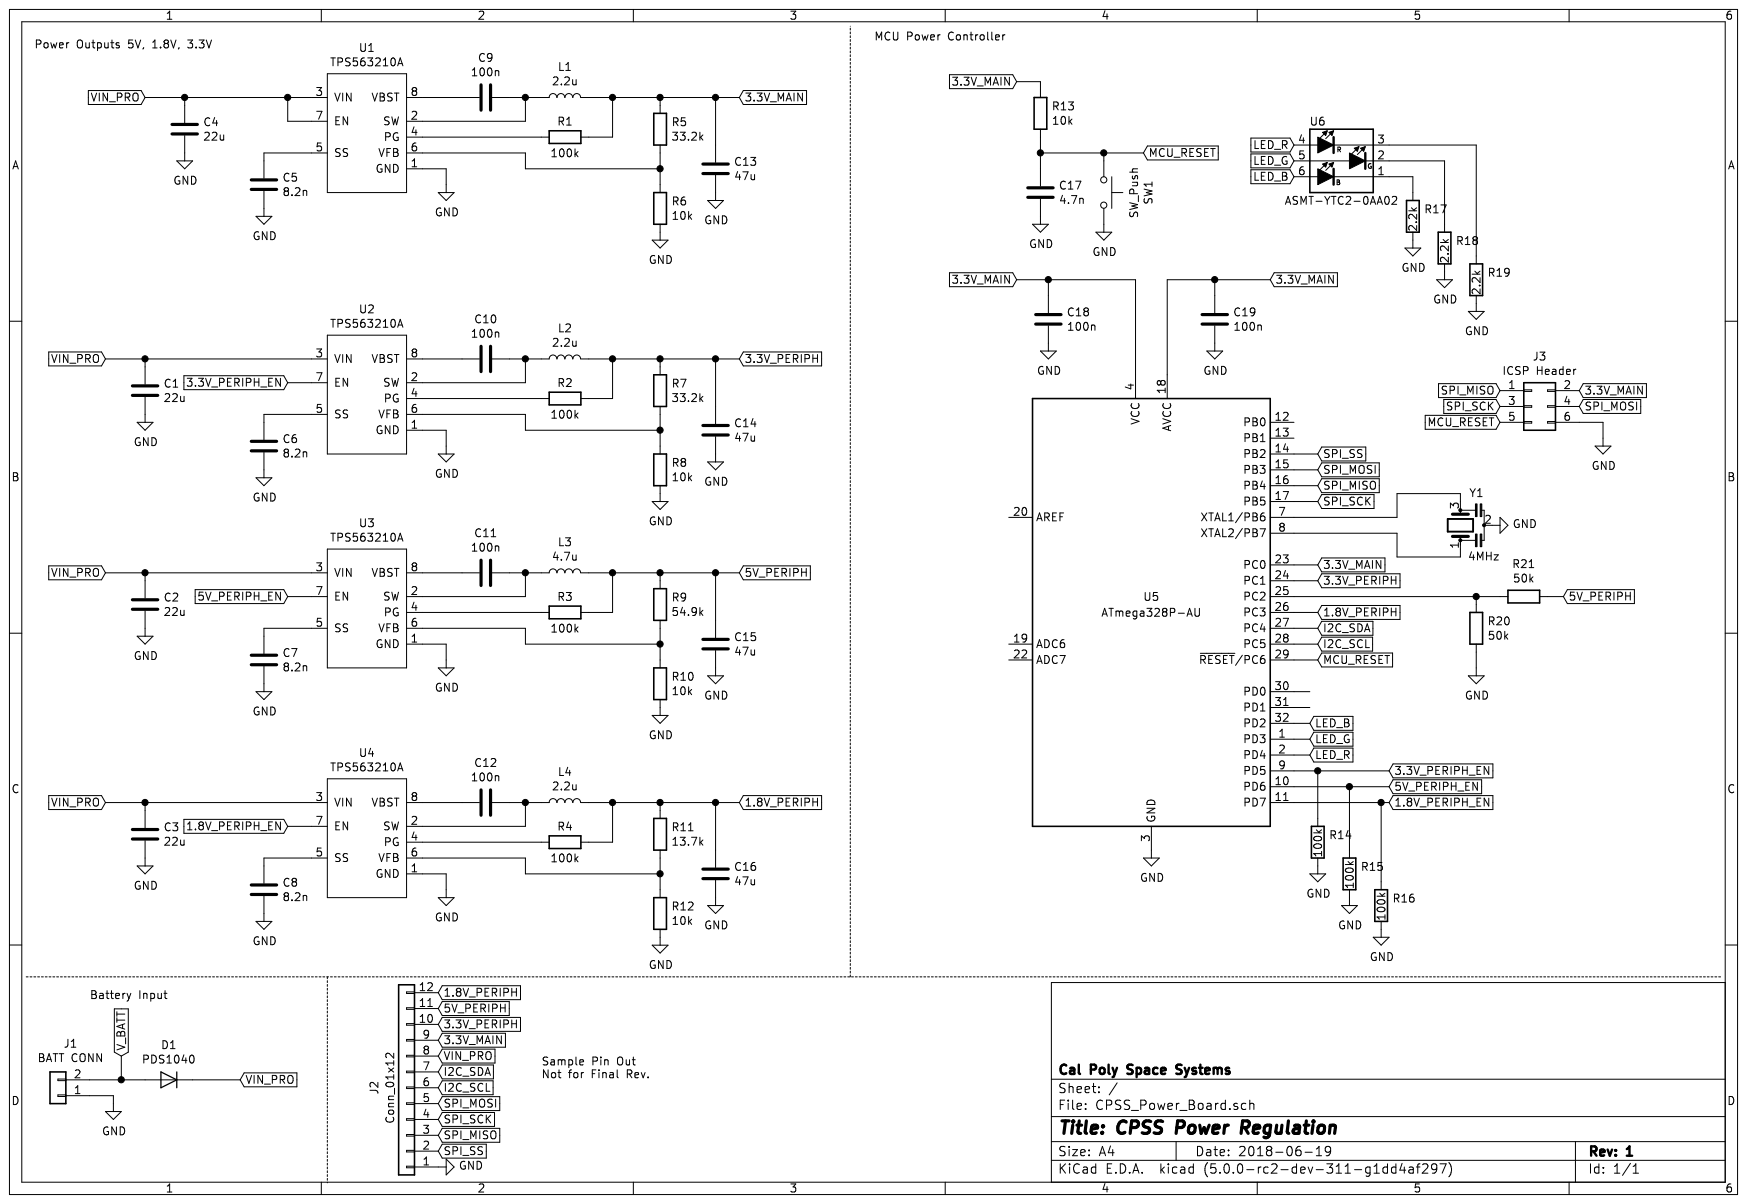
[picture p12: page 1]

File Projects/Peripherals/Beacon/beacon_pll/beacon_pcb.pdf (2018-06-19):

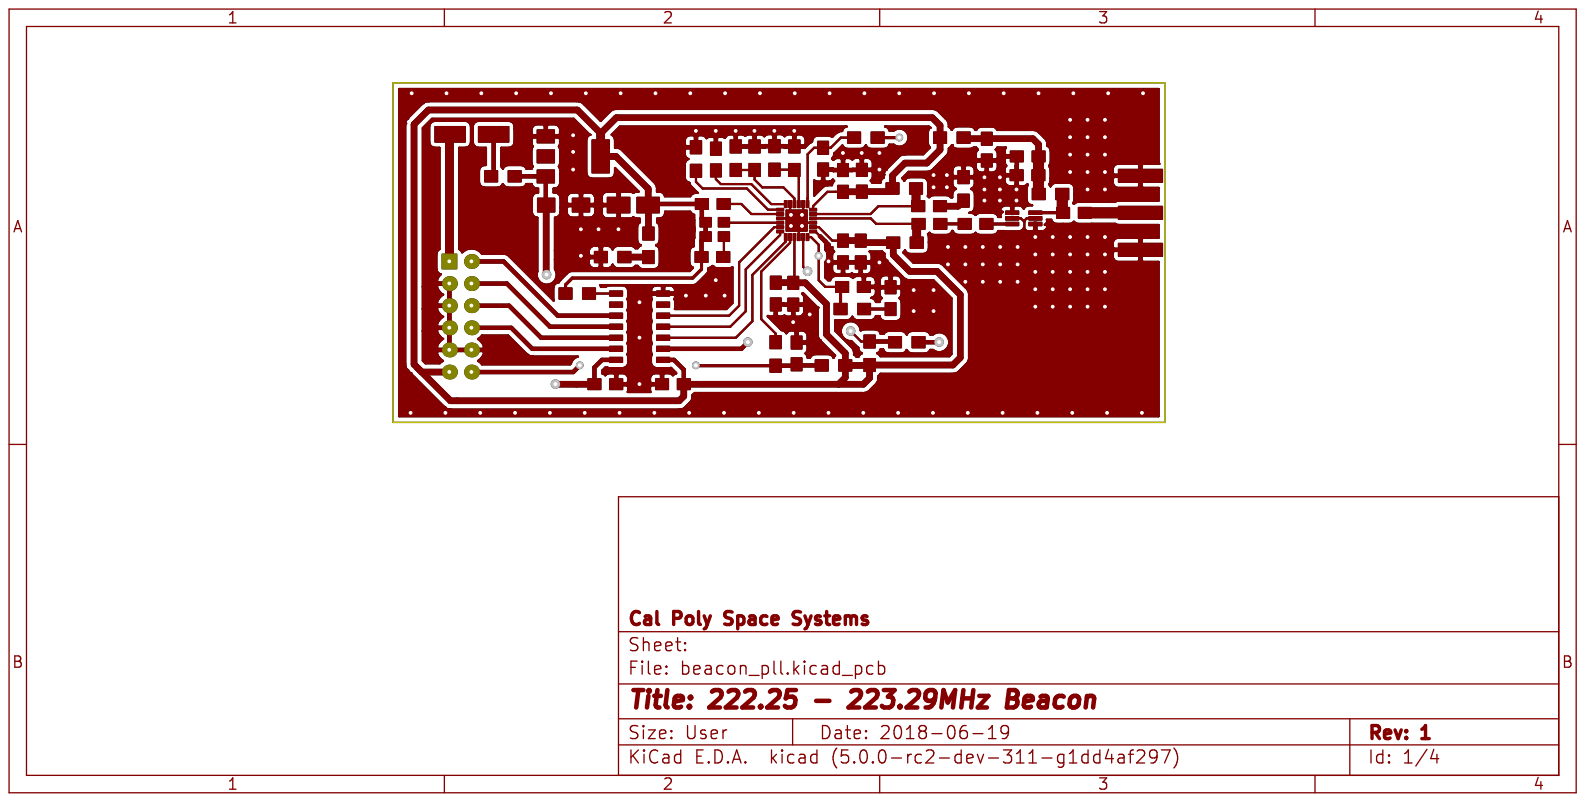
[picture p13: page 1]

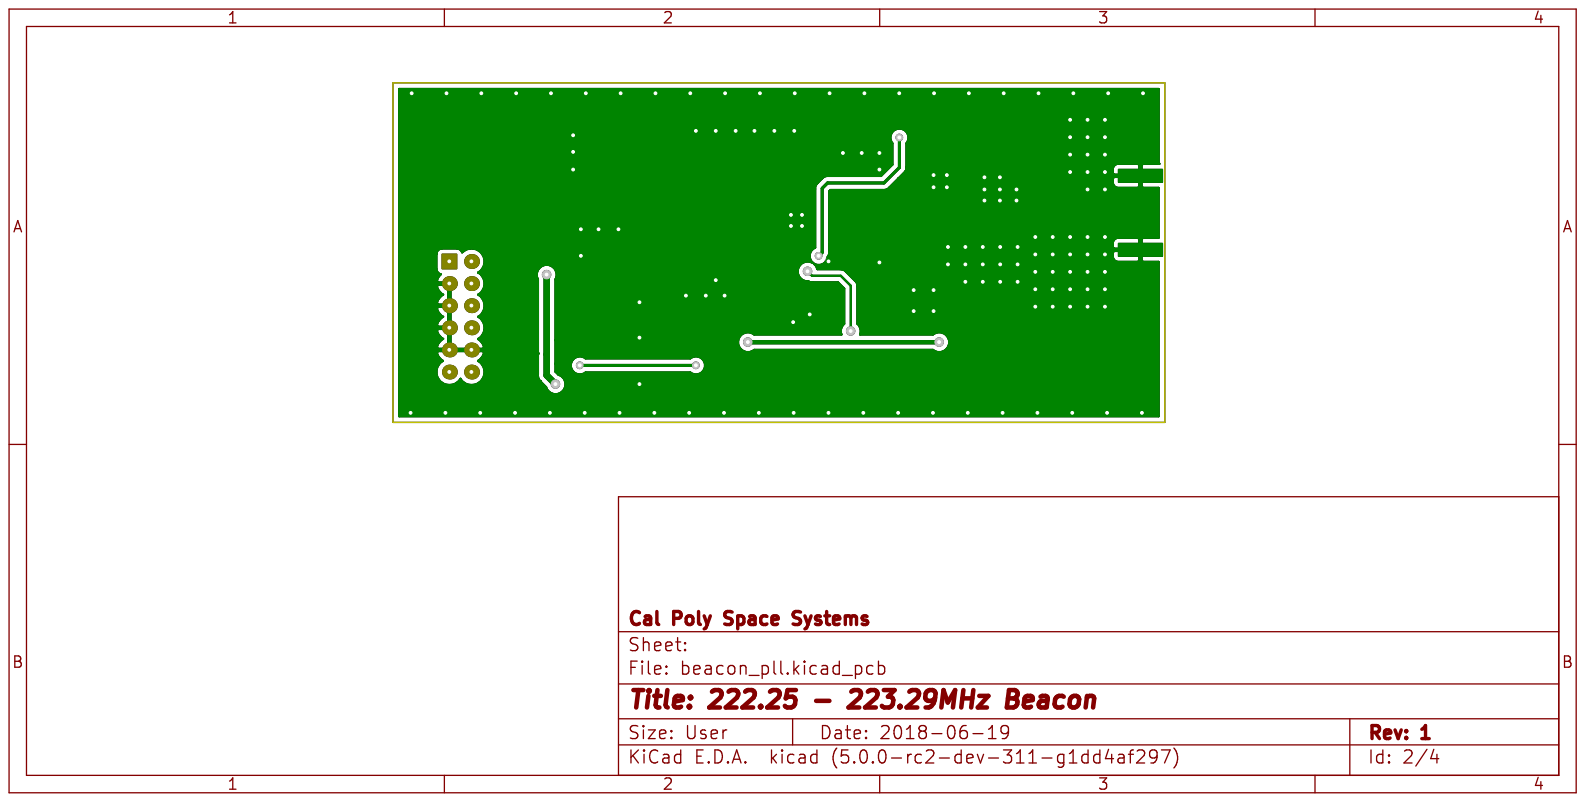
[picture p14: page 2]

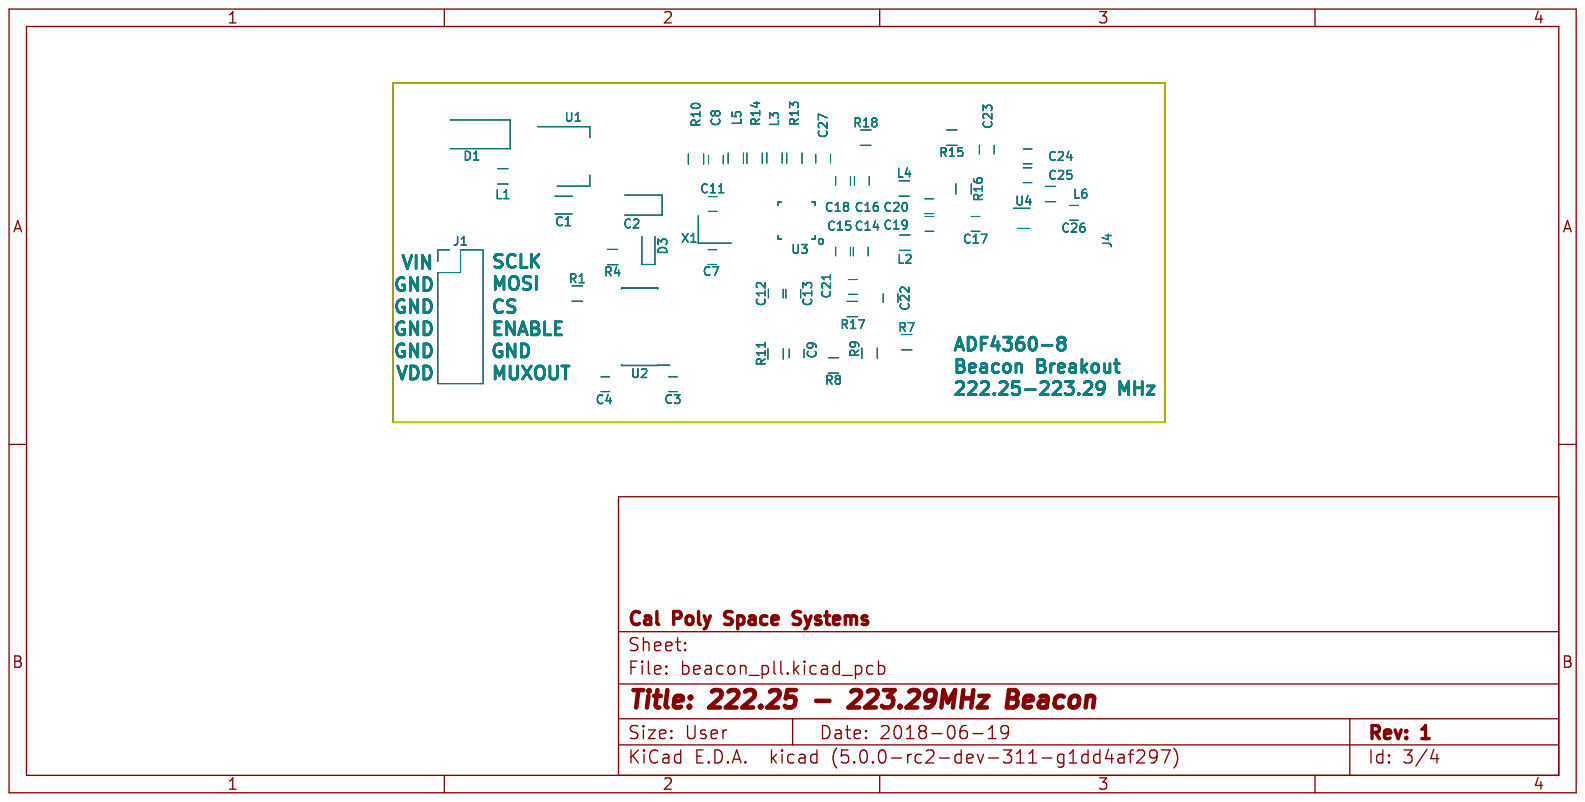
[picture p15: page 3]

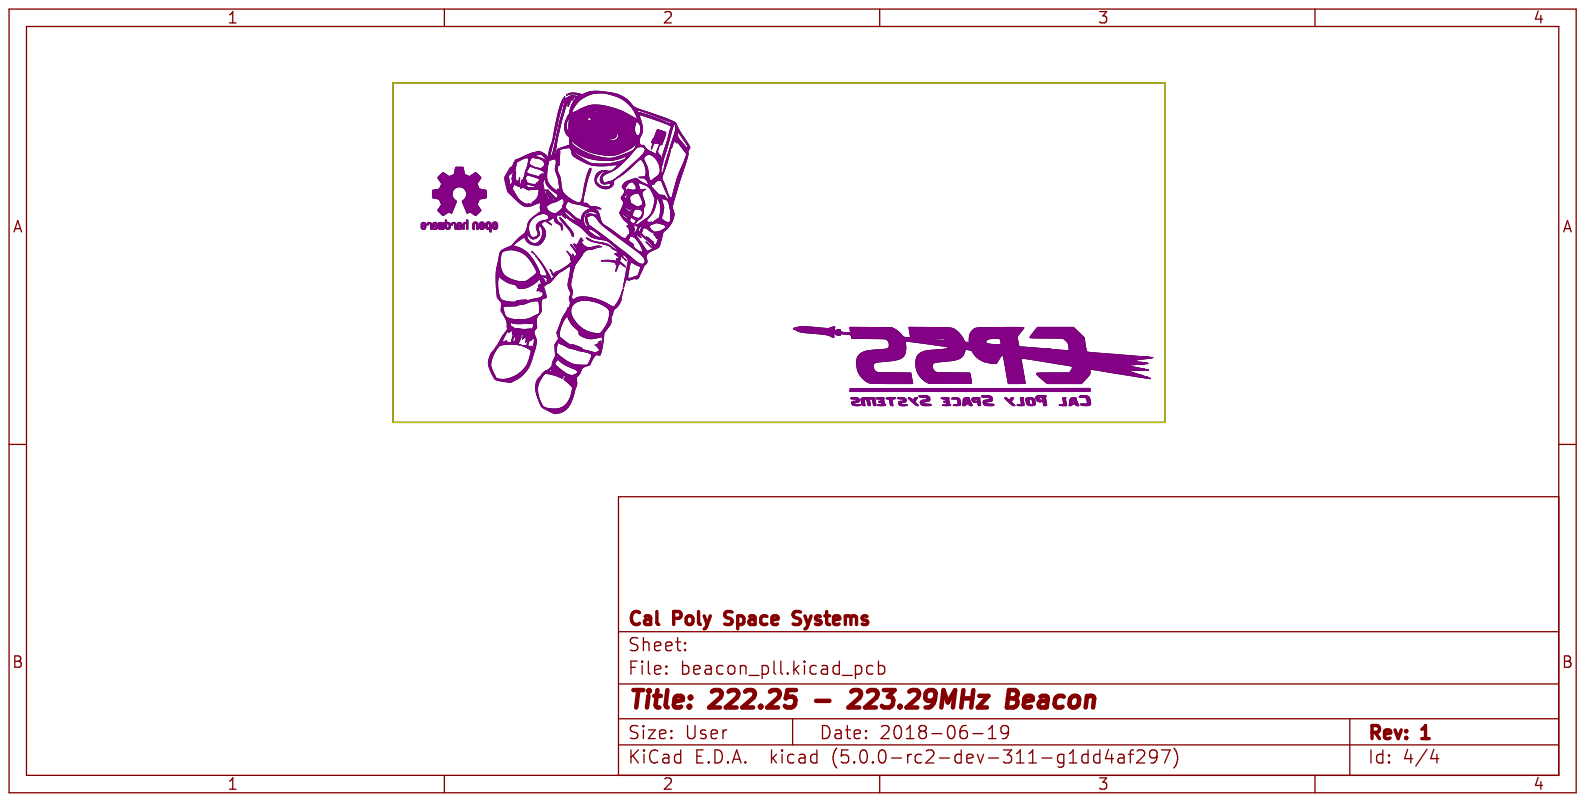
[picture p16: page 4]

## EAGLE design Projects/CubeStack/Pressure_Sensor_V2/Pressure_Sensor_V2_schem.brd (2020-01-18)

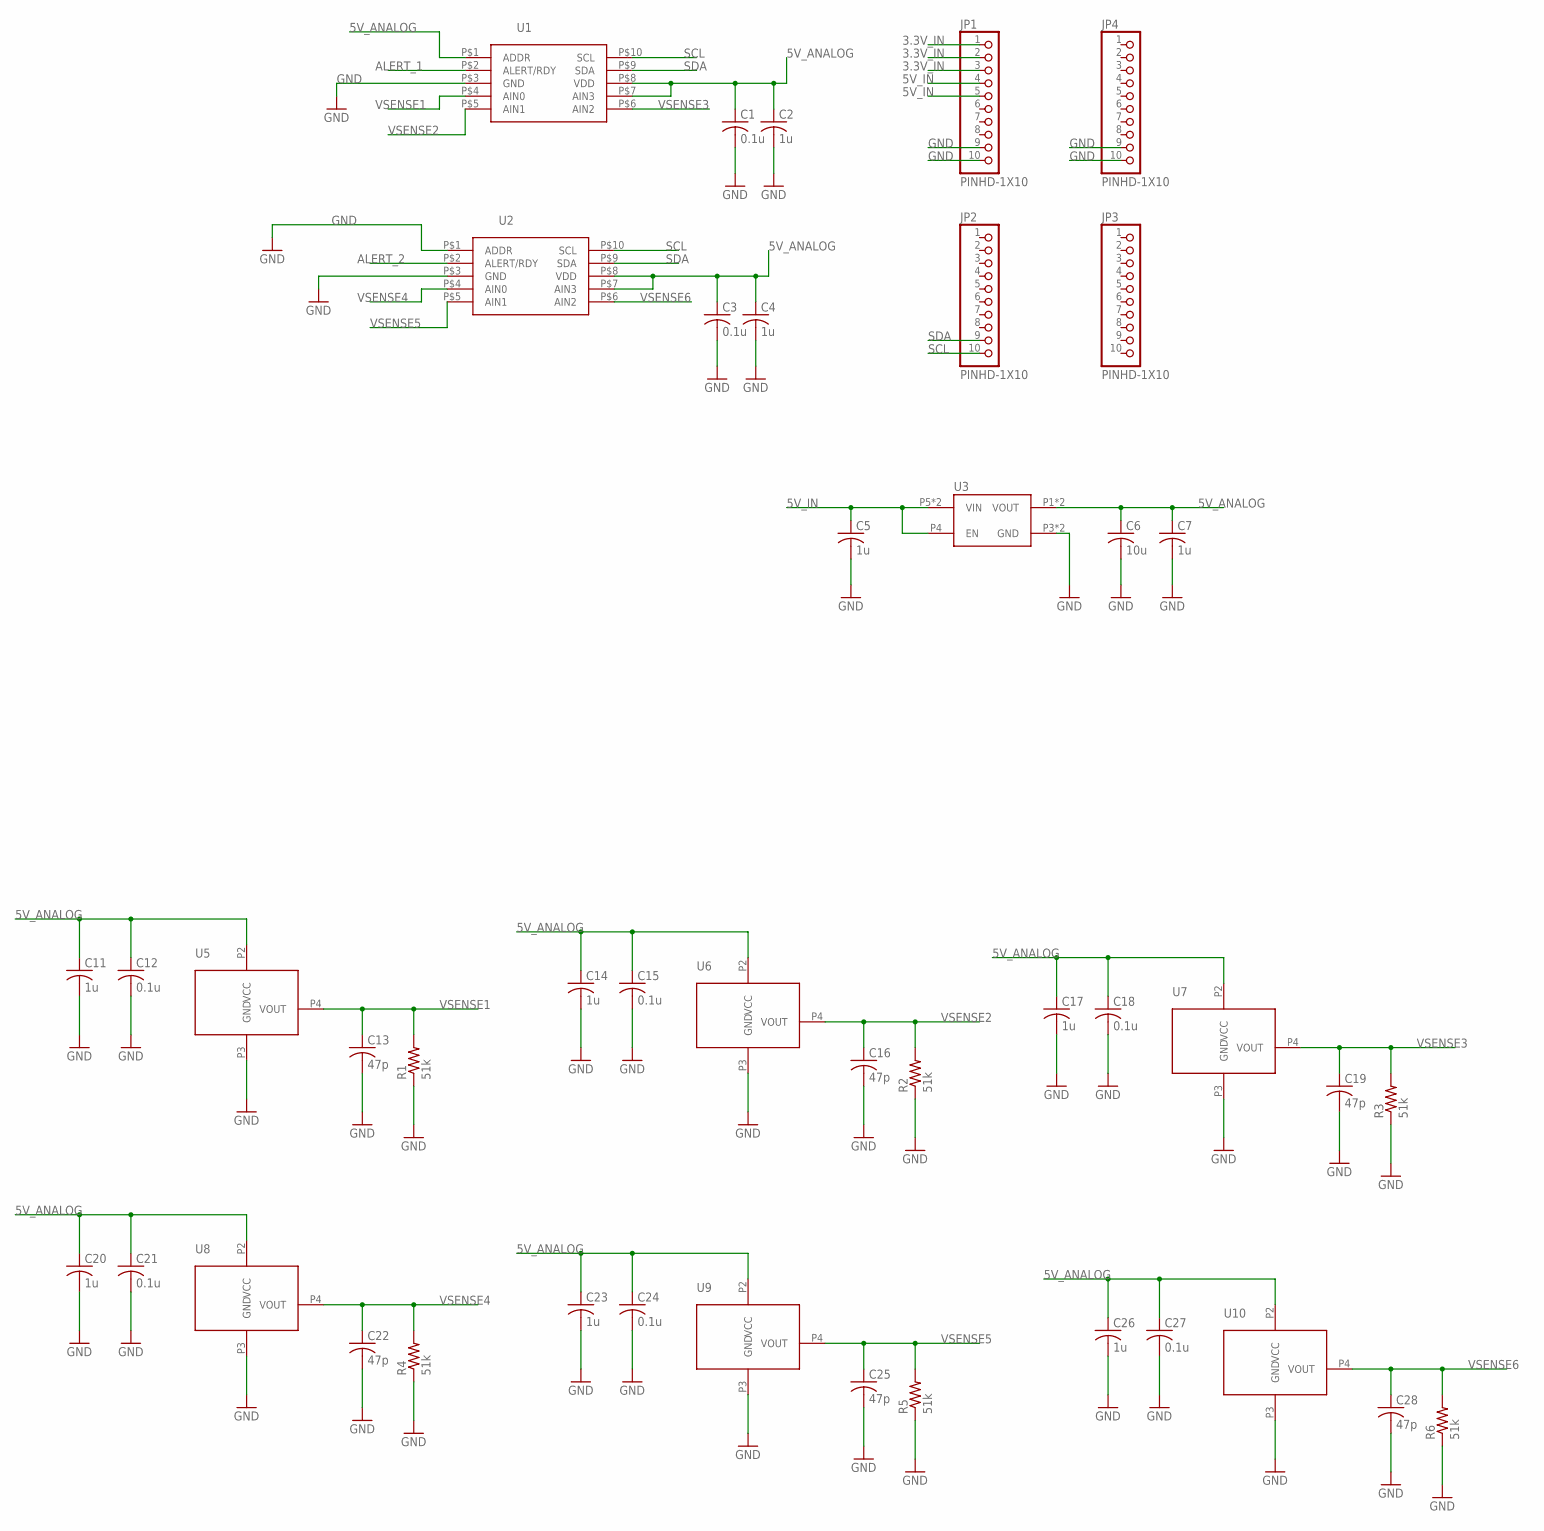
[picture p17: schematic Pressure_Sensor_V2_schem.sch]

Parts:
C1, C3, C12, C15, C18, C21, C24, C27: 0.1u; C0805
C2, C4, C5, C7, C11, C14, C17, C20, C23, C26: 1u; C0805
C6: 10u; C0805
C13, C16, C19, C22, C25, C28: 47p; C0805
JP1, JP2, JP3, JP4: PINHD-1X10; 1X10-BIG
R1, R2, R3, R4, R5, R6: 51k; R0805
U1, U2: ADS1115VSSOP; VSSOP-10
U3: ADP196; WLCSP
U5, U6, U7, U8, U9, U10: MPXH6400A; SSOP

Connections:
3.3V_IN: JP1.1, JP1.2, JP1.3
5V_ANALOG: C1.1, C2.1, C3.1, C4.1, C6.1, C7.1, C11.1, C12.1, C14.1, C15.1, C17.1, C18.1, C20.1, C21.1, C23.1, C24.1, C26.1, C27.1, U1.P$1 (ADDR), U1.P$7 (AIN3), U1.P$8 (VDD), U2.P$7 (AIN3), U2.P$8 (VDD), U3.P1 (VOUT), U3.P2 (VOUT), U5.P2 (VCC), U6.P2 (VCC), U7.P2 (VCC), U8.P2 (VCC), U9.P2 (VCC), U10.P2 (VCC)
5V_IN: C5.1, JP1.4, JP1.5, U3.P4 (EN), U3.P5 (VIN), U3.P6 (VIN)
ALERT_1: U1.P$2 (ALERT/RDY)
ALERT_2: U2.P$2 (ALERT/RDY)
GND: C1.2, C2.2, C3.2, C4.2, C5.2, C6.2, C7.2, C11.2, C12.2, C13.2, C14.2, C15.2, C16.2, C17.2, C18.2, C19.2, C20.2, C21.2, C22.2, C23.2, C24.2, C25.2, C26.2, C27.2, C28.2, JP1.9, JP1.10, JP4.9, JP4.10, R1.1, R2.1, R3.1, R4.1, R5.1, R6.1, U1.P$3 (GND), U2.P$1 (ADDR), U2.P$3 (GND), U3.P3 (GND), U3.TH (GND), U5.P3 (GND), U6.P3 (GND), U7.P3 (GND), U8.P3 (GND), U9.P3 (GND), U10.P3 (GND)
SCL: JP2.10, U1.P$10 (SCL), U2.P$10 (SCL)
SDA: JP2.9, U1.P$9 (SDA), U2.P$9 (SDA)
VSENSE1: C13.1, R1.2, U1.P$4 (AIN0), U5.P4 (VOUT)
VSENSE2: C16.1, R2.2, U1.P$5 (AIN1), U6.P4 (VOUT)
VSENSE3: C19.1, R3.2, U1.P$6 (AIN2), U7.P4 (VOUT)
VSENSE4: C22.1, R4.2, U2.P$4 (AIN0), U8.P4 (VOUT)
VSENSE5: C25.1, R5.2, U2.P$5 (AIN1), U9.P4 (VOUT)
VSENSE6: C28.1, R6.2, U2.P$6 (AIN2), U10.P4 (VOUT)

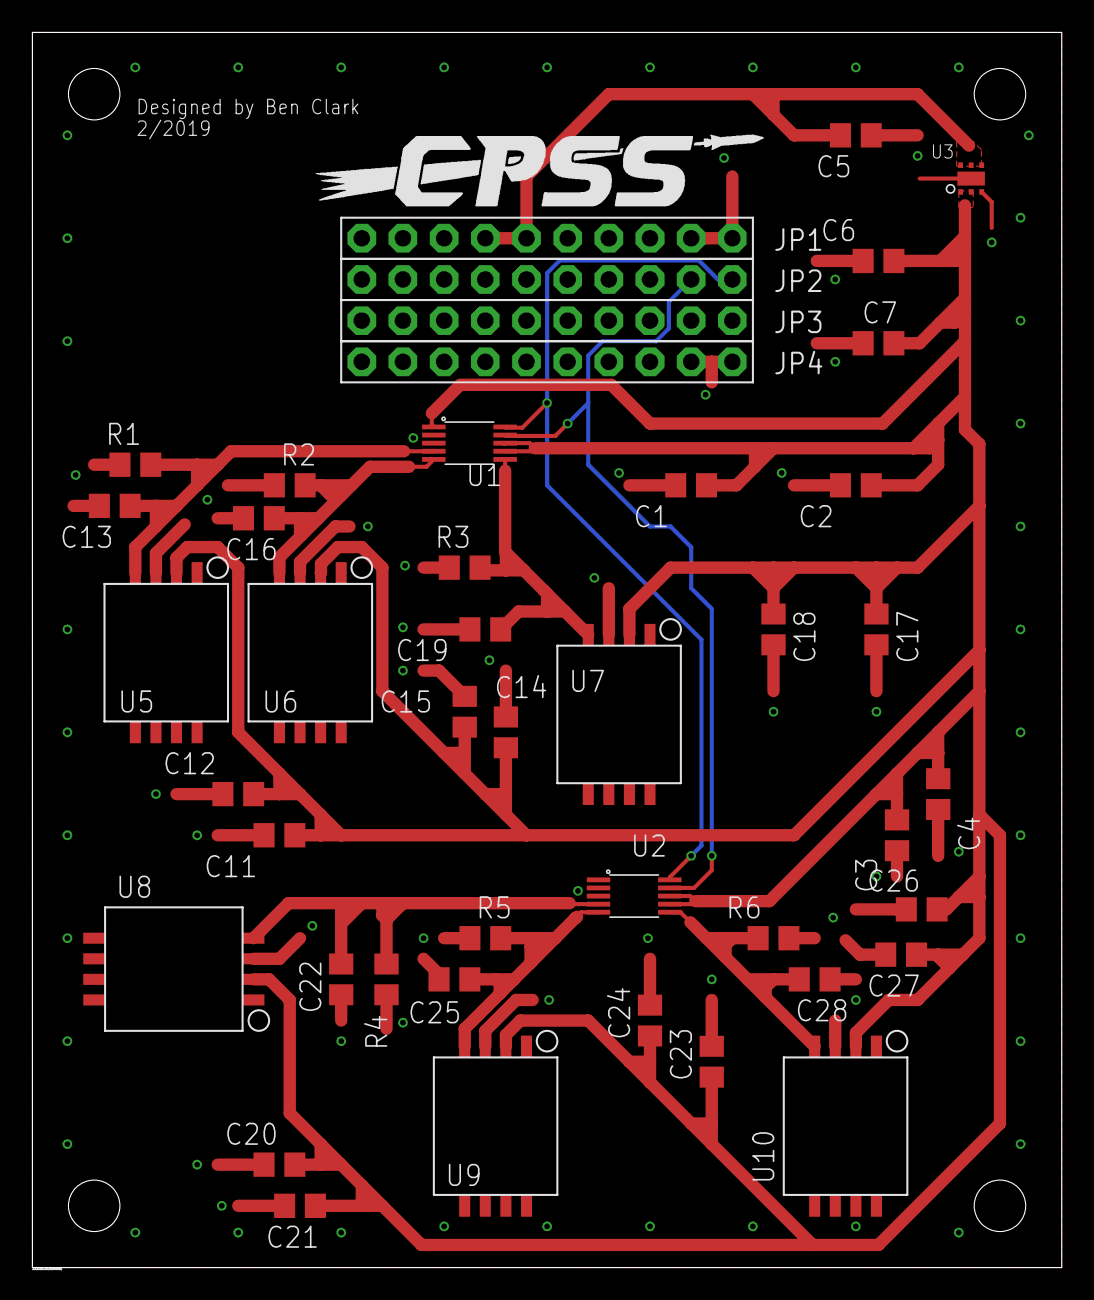
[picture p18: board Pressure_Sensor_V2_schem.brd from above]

Board: 2 copper layers, 63.5 x 76.2 mm, 44 parts (0 on the bottom side), 12 nets.

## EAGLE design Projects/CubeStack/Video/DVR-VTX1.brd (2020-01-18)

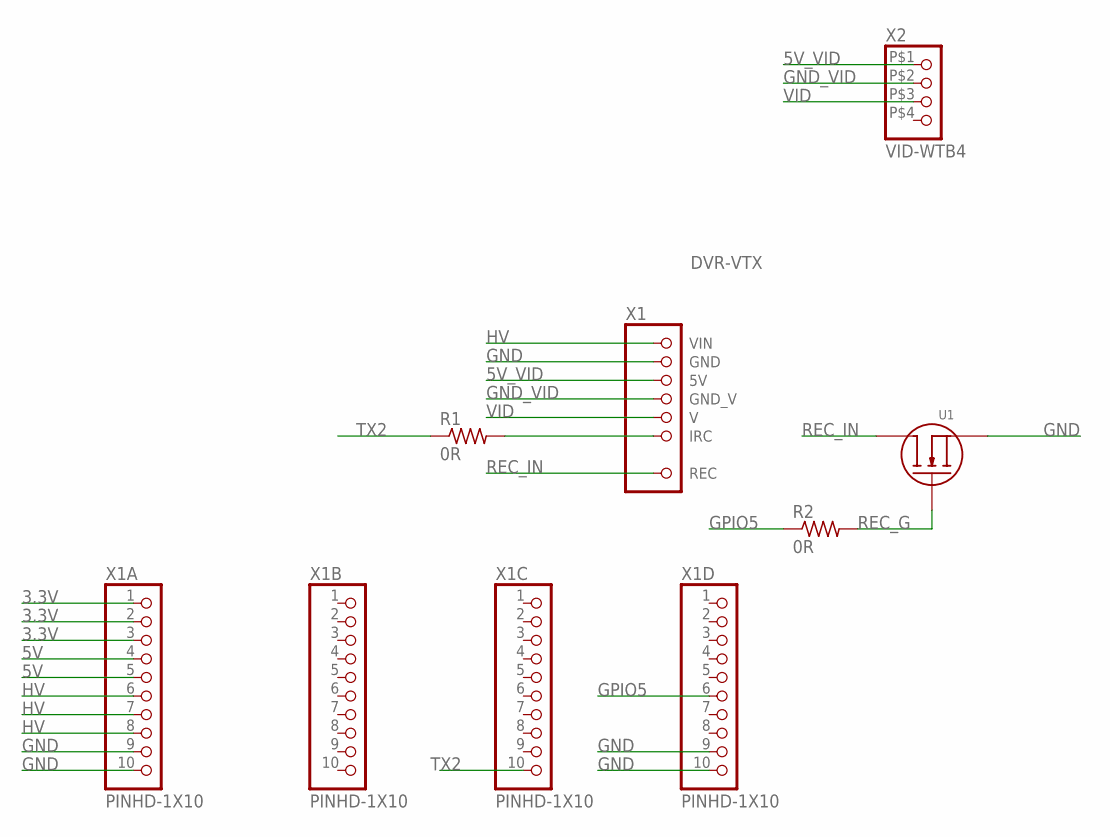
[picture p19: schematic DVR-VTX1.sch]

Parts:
R1, R2: 0R; R0603
U1: 2N7002E; NMINI3-R1-B
X1: DVR-VTX
X1A, X1B, X1C, X1D: PINHD-1X10; 1X10-BIG
X2: VID-WTB4; 10114829-10104LF

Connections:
3.3V: X1A.1, X1A.2, X1A.3
5V: X1A.4, X1A.5
5V_VID: X1.P$3 (5V), X2.P$1 (1)
GND: U1.2 (S), X1.P$2 (GND), X1A.9, X1A.10, X1D.9, X1D.10
GND_VID: X1.P$4 (GND_V), X2.P$2 (2)
GPIO5: R2.1, X1D.6
HV: X1.P$1 (VIN), X1A.6, X1A.7, X1A.8
REC_G: R2.2, U1.1 (G)
REC_IN: U1.3 (D), X1.P$7 (REC)
TRAMP: R1.2, X1.P$6 (IRC)
TX2: R1.1, X1C.10
VID: X1.P$5 (V), X2.P$3 (3)

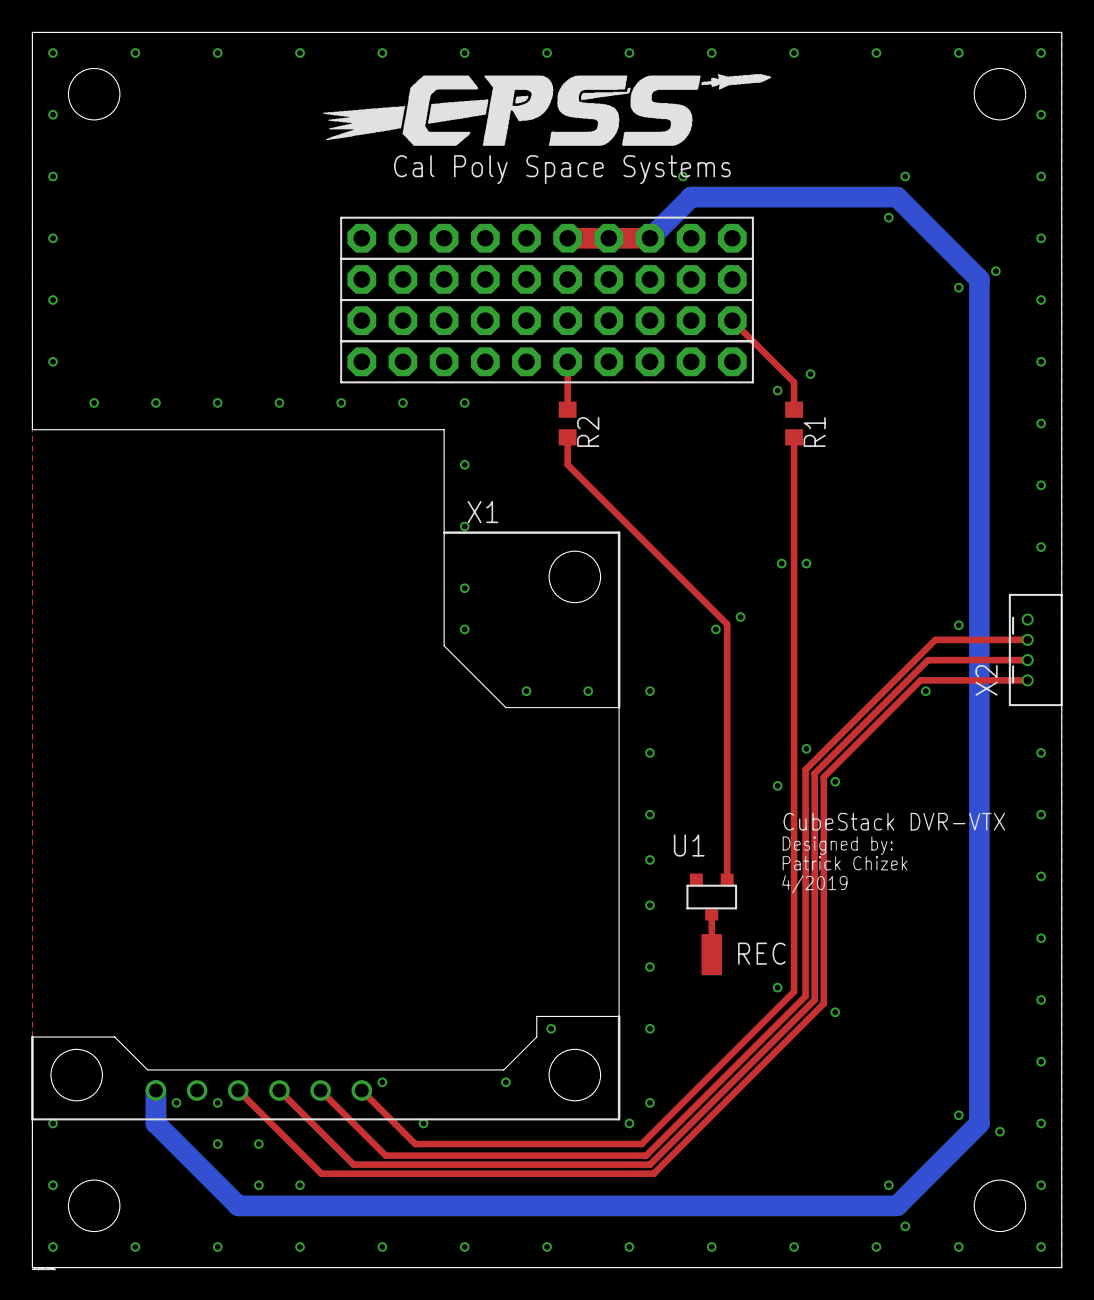
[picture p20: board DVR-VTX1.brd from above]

Board: 2 copper layers, 63.5 x 76.2 mm, 9 parts (0 on the bottom side), 12 nets.

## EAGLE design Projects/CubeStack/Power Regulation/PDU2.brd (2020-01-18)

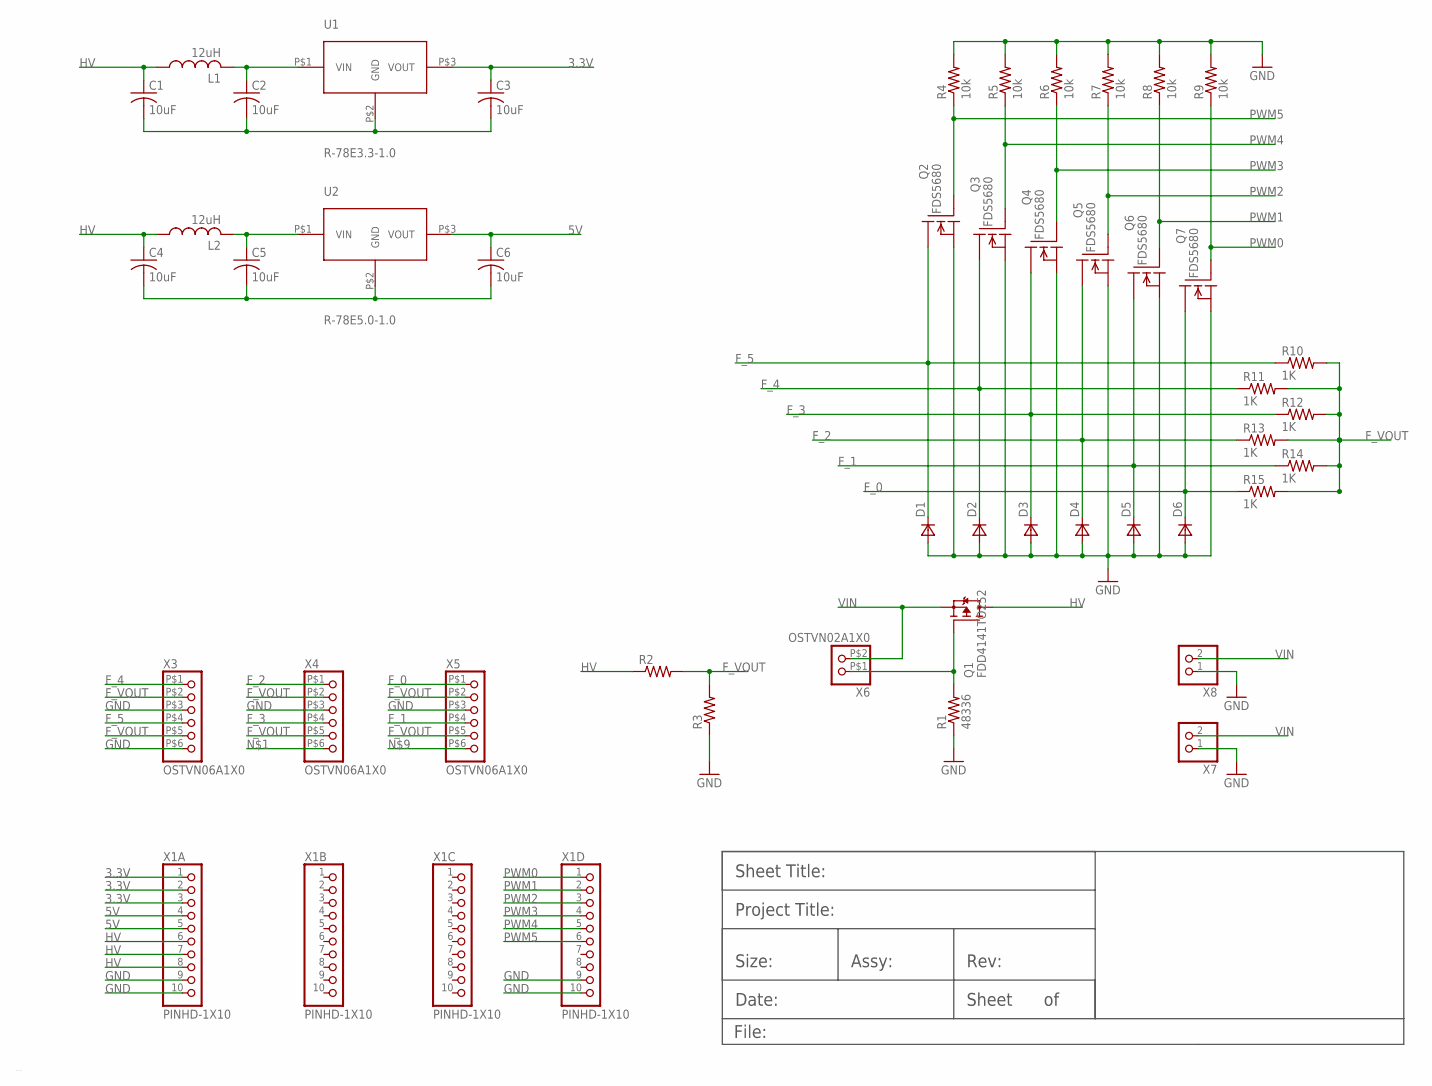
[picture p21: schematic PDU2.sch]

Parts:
C1, C2, C3, C4, C5, C6: 10uF; C1206
D1, D2, D3, D4, D5, D6: DSOD323; SOD323
L1, L2: 12uH; L2012C
Q1: FDD4141TO252; TO252
Q2, Q3, Q4, Q5, Q6, Q7: FDS5680; SO-8
R1: 48336; R1206
R2, R3: R-US_R6332; R6332
R4, R5, R6, R7, R8, R9: 10k; R0603
R10, R11, R12, R13, R14, R15: 1K; R0603
U1: R-78E3.3-1.0; R-78E-1.0
U2: R-78E5.0-1.0; R-78E-1.0
X1A, X1B, X1C, X1D: PINHD-1X10; 1X10-BIG
X3, X4, X5: OSTVN06A1X0
X6: OSTVN02A1X0
X7, X8: PINHD-1X2/90; 1X02/90

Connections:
3.3V: C3.1, U1.P$3 (VOUT), X1A.1, X1A.2, X1A.3
5V: C6.1, U2.P$3 (VOUT), X1A.4, X1A.5
EN: Q1.1 (G), R1.2, X6.P$1 (1)
F_0: D6.1 (C), Q7.5 (D), Q7.6 (D), Q7.7 (D), Q7.8 (D), R15.1, X5.P$1 (1)
F_1: D5.1 (C), Q6.5 (D), Q6.6 (D), Q6.7 (D), Q6.8 (D), R14.1, X5.P$4 (4)
F_2: D4.1 (C), Q5.5 (D), Q5.6 (D), Q5.7 (D), Q5.8 (D), R13.1, X4.P$1 (1)
F_3: D3.1 (C), Q4.5 (D), Q4.6 (D), Q4.7 (D), Q4.8 (D), R12.1, X4.P$4 (4)
F_4: D2.1 (C), Q3.5 (D), Q3.6 (D), Q3.7 (D), Q3.8 (D), R11.1, X3.P$1 (1)
F_5: D1.1 (C), Q2.5 (D), Q2.6 (D), Q2.7 (D), Q2.8 (D), R10.1, X3.P$4 (4)
F_VOUT: R2.2, R3.2, R10.2, R11.2, R12.2, R13.2, R14.2, R15.2, X3.P$2 (2), X3.P$5 (5), X4.P$2 (2), X4.P$5 (5), X5.P$2 (2), X5.P$5 (5)
GND: C1.2, C2.2, C3.2, C4.2, C5.2, C6.2, D1.2 (A), D2.2 (A), D3.2 (A), D4.2 (A), D5.2 (A), D6.2 (A), Q2.1 (S), Q2.2 (S), Q2.3 (S), Q3.1 (S), Q3.2 (S), Q3.3 (S), Q4.1 (S), Q4.2 (S), Q4.3 (S), Q5.1 (S), Q5.2 (S), Q5.3 (S), Q6.1 (S), Q6.2 (S), Q6.3 (S), Q7.1 (S), Q7.2 (S), Q7.3 (S), R1.1, R3.1, R4.2, R5.2, R6.2, R7.2, R8.2, R9.2, U1.P$2 (GND), U2.P$2 (GND), X1A.9, X1A.10, X1D.9, X1D.10, X3.P$3 (3), X3.P$6 (6), X4.P$3 (3), X5.P$3 (3), X7.1, X8.1
HV: C1.1, C4.1, L1.1, L2.1, Q1.3 (D), R2.1, X1A.6, X1A.7, X1A.8
unnamed: C2.1, L1.2, U1.P$1 (VIN)
unnamed: C5.1, L2.2, U2.P$1 (VIN)
PWM0: Q7.4 (G), R9.1, X1D.1
PWM1: Q6.4 (G), R8.1, X1D.2
PWM2: Q5.4 (G), R7.1, X1D.3
PWM3: Q4.4 (G), R6.1, X1D.4
PWM4: Q3.4 (G), R5.1, X1D.5
PWM5: Q2.4 (G), R4.1, X1D.6
VIN: Q1.2 (S), X6.P$2 (2), X7.2, X8.2

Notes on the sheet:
C:/Users/patri/Pictures/CPSSLOGO.bmp

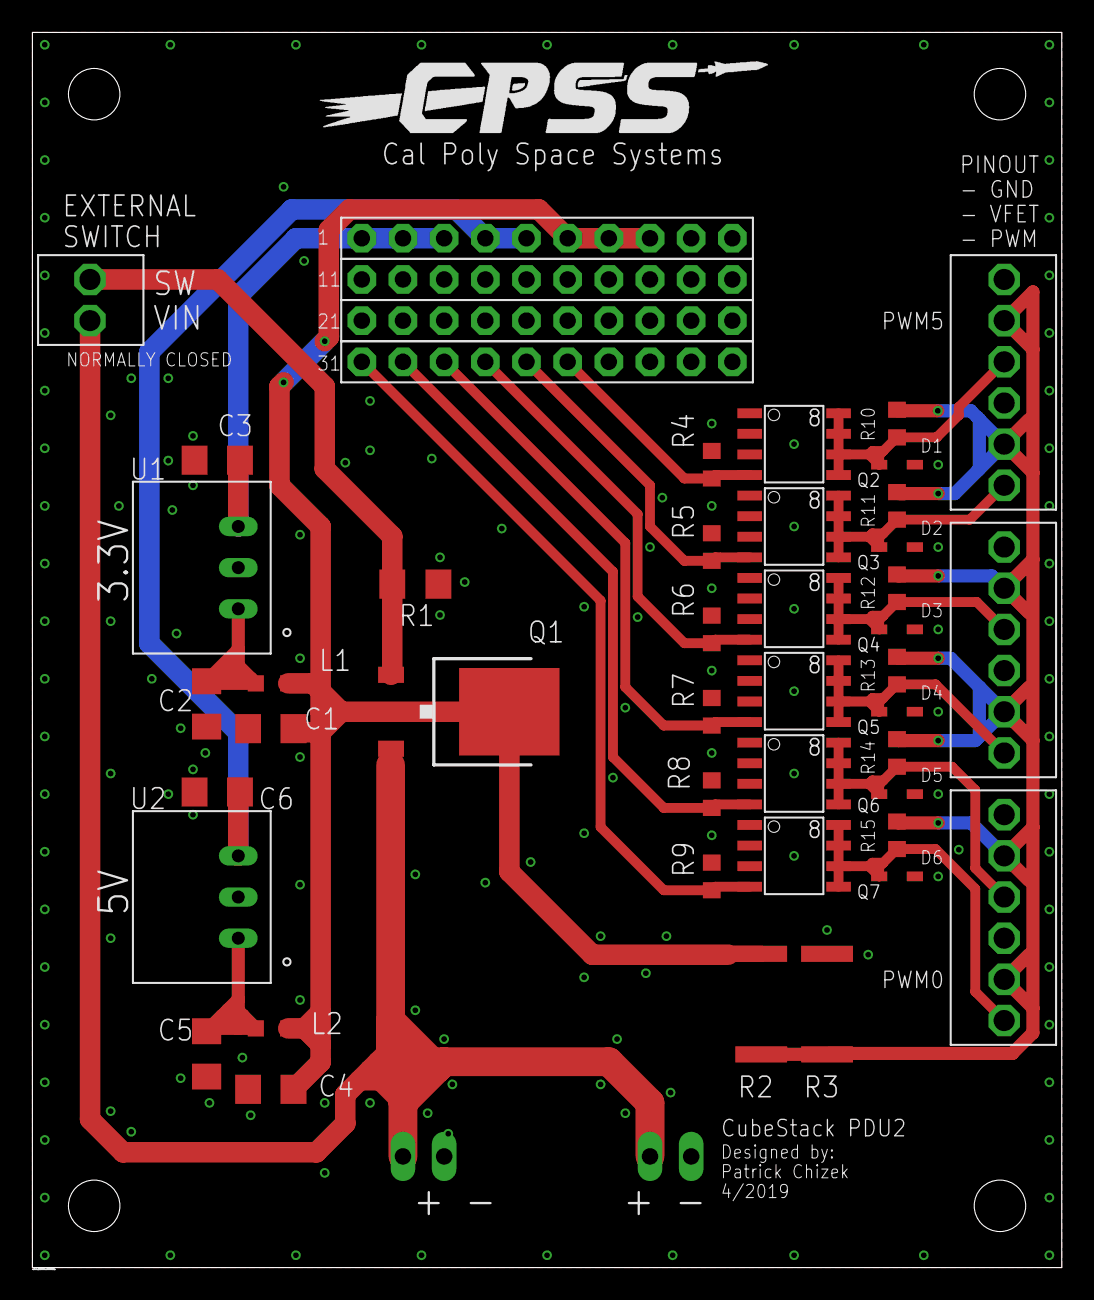
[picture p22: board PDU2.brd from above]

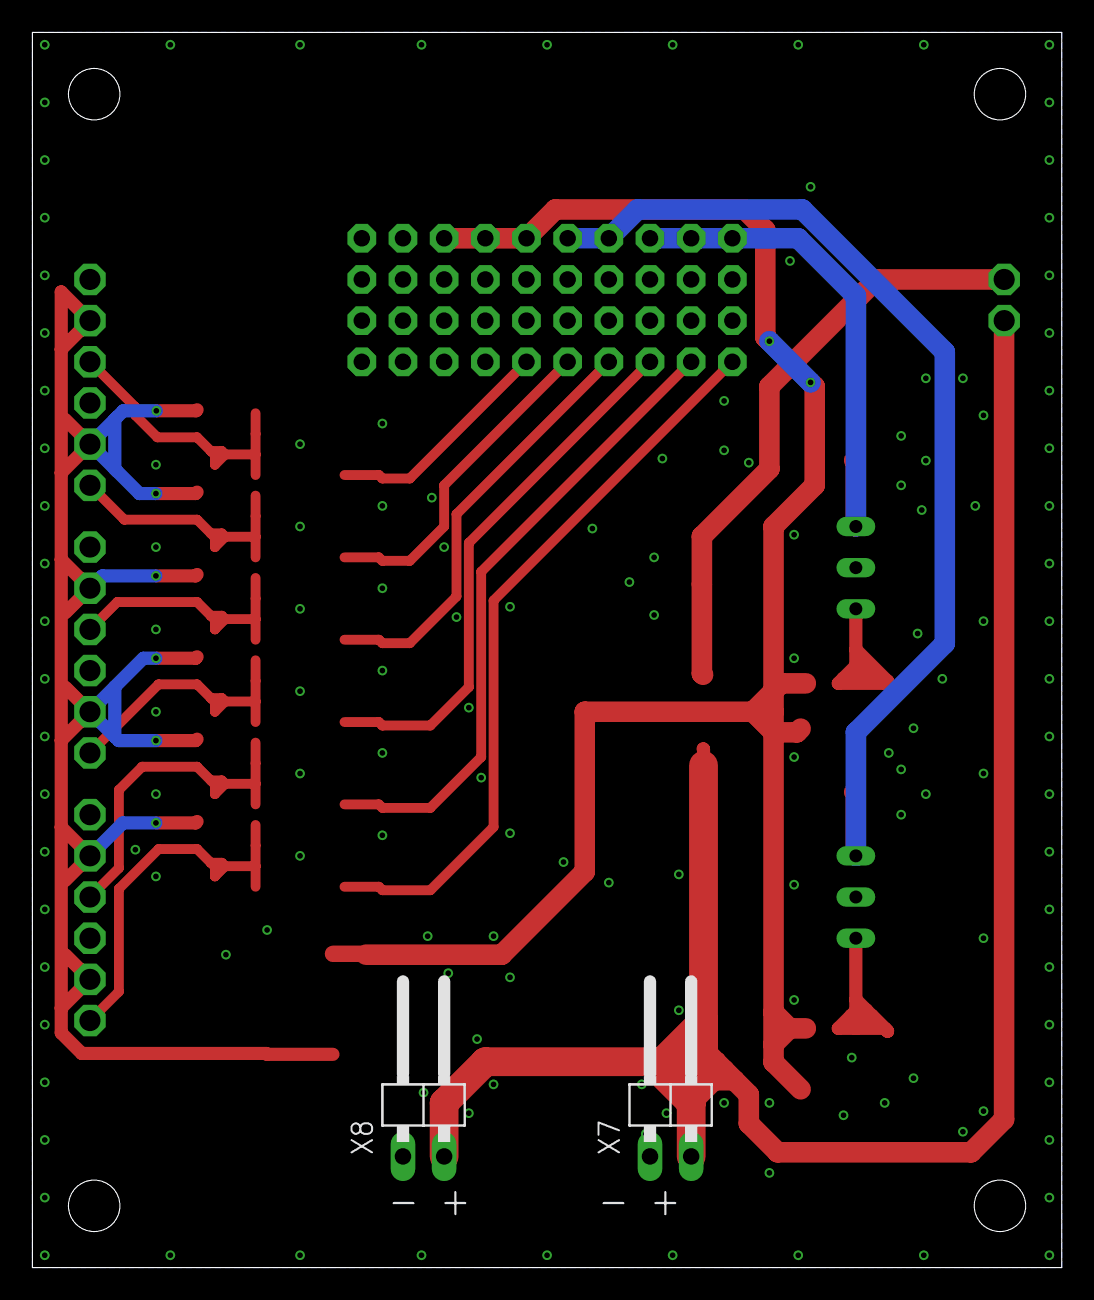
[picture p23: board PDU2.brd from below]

Board: 2 copper layers, 63.5 x 76.2 mm, 48 parts (2 on the bottom side), 21 nets.

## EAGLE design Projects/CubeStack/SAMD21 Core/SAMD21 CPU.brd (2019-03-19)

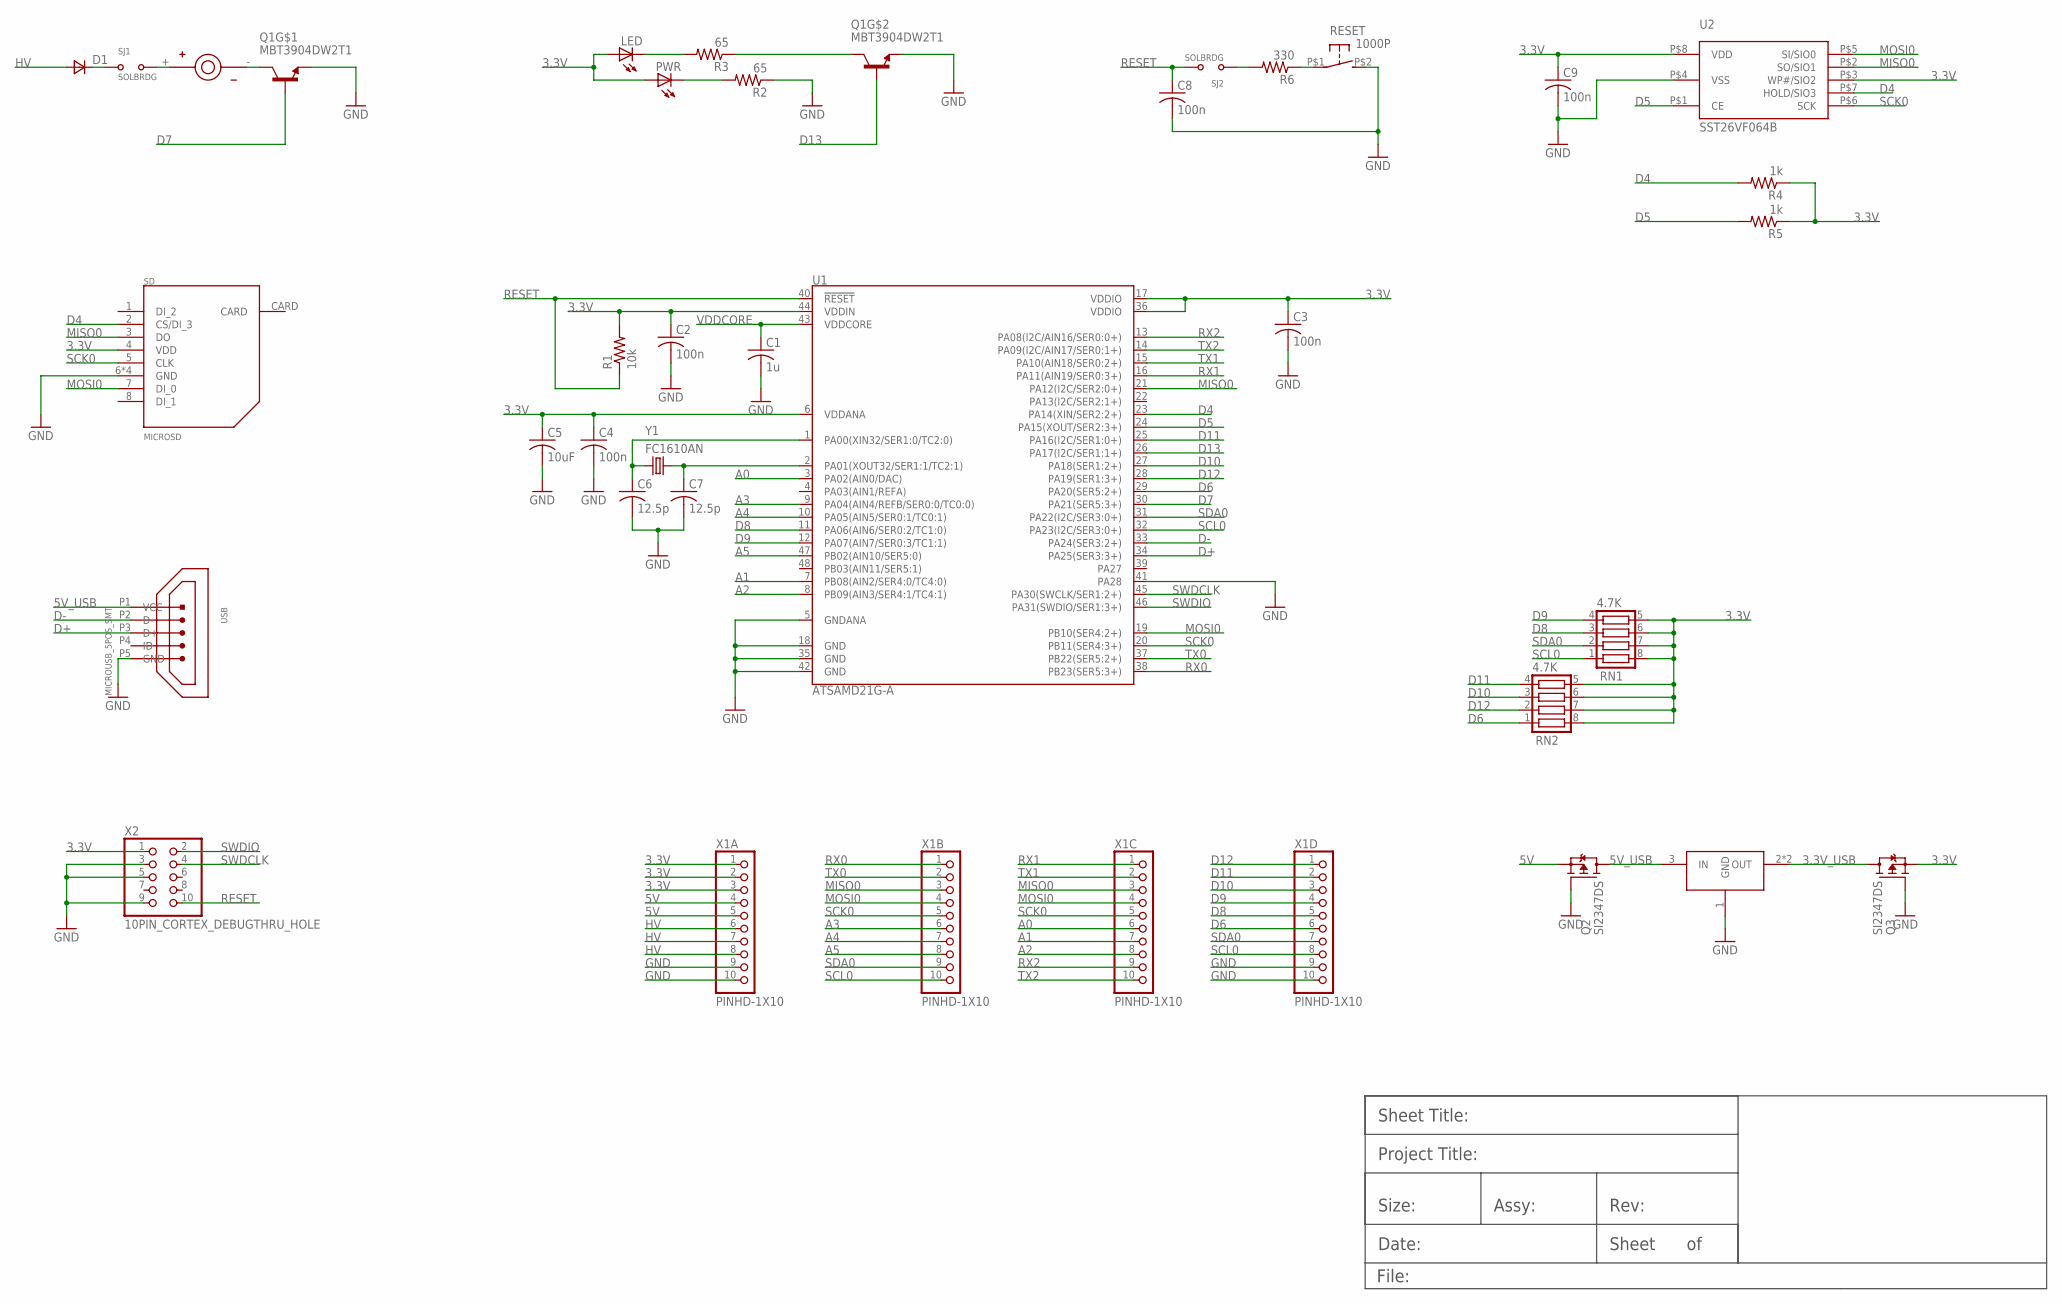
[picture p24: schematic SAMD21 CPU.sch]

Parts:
C1: 1u; C0603
C2, C3, C4, C8, C9: 100n; C0603
C5: 10uF; C0603
C6, C7: 12.5p; C0603
D1: DSOD323; SOD323
LED: LEDCHIPLED_0805; CHIPLED_0805
LS1: AI-1440-TWT-24V-2-R; AI-1440-TWT-24-2-R
PWR: LEDCHIPLED_0805; CHIPLED_0805
Q1: MBT3904DW2T1; SOT-363
Q2, Q3: SI2347DS; SOT23
R1: 10k; R0603
R2, R3: 65; R0603
R4, R5: 1k; R0603
R6: 330; R0603
RESET: 1000P; B3U-1000P
RN1, RN2: 4.7K; CTS742C083
SD: MICROSD; CONN_MICROSD
SJ1, SJ2: SOLBRDG
U1: ATSAMD21G-A; TQFP-48
U2: SST26VF064B; SOIJ
U3: AZ1117C; SOT89
USB: MICROUSB_5POS_SMT; RECPT_SMT_R/A
X1A, X1B, X1C, X1D: PINHD-1X10; 1X10-BIG
X2: 10PIN_CORTEX_DEBUGTHRU_HOLE; 2X5-PTH-1.27MM
Y1: FC1610AN; A431L

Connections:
3.3V: C2.1, C3.1, C4.1, C5.1, C9.1, LED.A, PWR.A, Q3.2 (S), R1.2, R4.1, R5.1, RN1.5, RN1.6, RN1.7, RN1.8, RN2.5, RN2.6, RN2.7, RN2.8, SD.4 (VDD), U1.6 (VDDANA), U1.17 (VDDIO), U1.36 (VDDIO), U1.44 (VDDIN), U2.P$3 (WP#/SIO2), U2.P$8 (VDD), X1A.1, X1A.2, X1A.3, X2.1
3.3V_USB: Q3.3 (D), U3.2 (OUT), U3.2@1 (OUT)
5V: Q2.2 (S), X1A.4, X1A.5
5V_USB: Q2.3 (D), U3.3 (IN), USB.P1 (VCC)
A0: U1.3 (PA02(AIN0/DAC)), X1C.6
A1: U1.7 (PB08(AIN2/SER4:0/TC4:0)), X1C.7
A2: U1.8 (PB09(AIN3/SER4:1/TC4:1)), X1C.8
A3: U1.9 (PA04(AIN4/REFB/SER0:0/TC0:0)), X1B.6
A4: U1.10 (PA05(AIN5/SER0:1/TC0:1)), X1B.7
A5: U1.47 (PB02(AIN10/SER5:0)), X1B.8
D4: R4.2, SD.2 (CS/DI_3), U1.23 (PA14(XIN/SER2:2+)), U2.P$7 (HOLD/SIO3)
D5: R5.2, U1.24 (PA15(XOUT/SER2:3+)), U2.P$1 (CE)
D6: RN2.1, U1.29 (PA20(SER5:2+)), X1D.6
D7: Q1.P$2 (B), U1.30 (PA21(SER5:3+))
D8: RN1.3, U1.11 (PA06(AIN6/SER0:2/TC1:0)), X1D.5
D9: RN1.4, U1.12 (PA07(AIN7/SER0:3/TC1:1)), X1D.4
D10: RN2.3, U1.27 (PA18(SER1:2+)), X1D.3
D11: RN2.4, U1.25 (PA16(I2C/SER1:0+)), X1D.2
D12: RN2.2, U1.28 (PA19(SER1:3+)), X1D.1
D13: Q1.P$1 (B), U1.26 (PA17(I2C/SER1:1+))
D+: U1.34 (PA25(SER3:3+)), USB.P3 (D+)
D-: U1.33 (PA24(SER3:2+)), USB.P2 (D-)
GND: C1.2, C2.2, C3.2, C4.2, C5.2, C6.2, C7.2, C8.2, C9.2, Q1.P$3 (E), Q1.P$6 (E), Q2.1 (G), Q3.1 (G), R2.1, RESET.P$2 (S), SD.6 (GND), SD.GND1 (GND), SD.GND2 (GND), SD.GND3 (GND), U1.5 (GNDANA), U1.18 (GND), U1.35 (GND), U1.41 (PA28), U1.42 (GND), U2.P$4 (VSS), U3.1 (GND), USB.P5 (GND), X1A.9, X1A.10, X1D.9, X1D.10, X2.3, X2.5, X2.9
HV: D1.2 (A), X1A.6, X1A.7, X1A.8
LS_D: LS1.-, Q1.P$4 (C)
L_3: LED.C, R3.2
L_3_D: Q1.P$5 (C), R3.1
MISO0: SD.3 (DO), U1.21 (PA12(I2C/SER2:0+)), U2.P$2 (SO/SIO1), X1B.3, X1C.3
MOSI0: SD.7 (DI_0), U1.19 (PB10(SER4:2+)), U2.P$5 (SI/SIO0), X1B.4, X1C.4
unnamed: C6.1, U1.1 (PA00(XIN32/SER1:0/TC2:0)), Y1.P$1 (1)
unnamed: C7.1, U1.2 (PA01(XOUT32/SER1:1/TC2:1)), Y1.P$2 (2)
unnamed: R6.2, SJ2.P$1
unnamed: LS1.+, SJ1.P$2
unnamed: PWR.C, R2.2
unnamed: R6.1, RESET.P$1
unnamed: D1.1 (C), SJ1.P$1
RESET: C8.1, R1.1, SJ2.P$2, U1.40 (!RESET!), X2.10
RX0: U1.38 (PB23(SER5:3+)), X1B.1
RX1: U1.16 (PA11(AIN19/SER0:3+)), X1C.1
RX2: U1.13 (PA08(I2C/AIN16/SER0:0+)), X1C.9
SCK0: SD.5 (CLK), U1.20 (PB11(SER4:3+)), U2.P$6 (SCK), X1B.5, X1C.5
SCL0: RN1.1, U1.32 (PA23(I2C/SER3:0+)), X1B.10, X1D.8
SDA0: RN1.2, U1.31 (PA22(I2C/SER3:0+)), X1B.9, X1D.7
SWDCLK: U1.45 (PA30(SWCLK/SER1:2+)), X2.4
SWDIO: U1.46 (PA31(SWDIO/SER1:3+)), X2.2
TX0: U1.37 (PB22(SER5:2+)), X1B.2
TX1: U1.15 (PA10(AIN18/SER0:2+)), X1C.2
TX2: U1.14 (PA09(I2C/AIN17/SER0:1+)), X1C.10
VDDCORE: C1.1, U1.43 (VDDCORE)

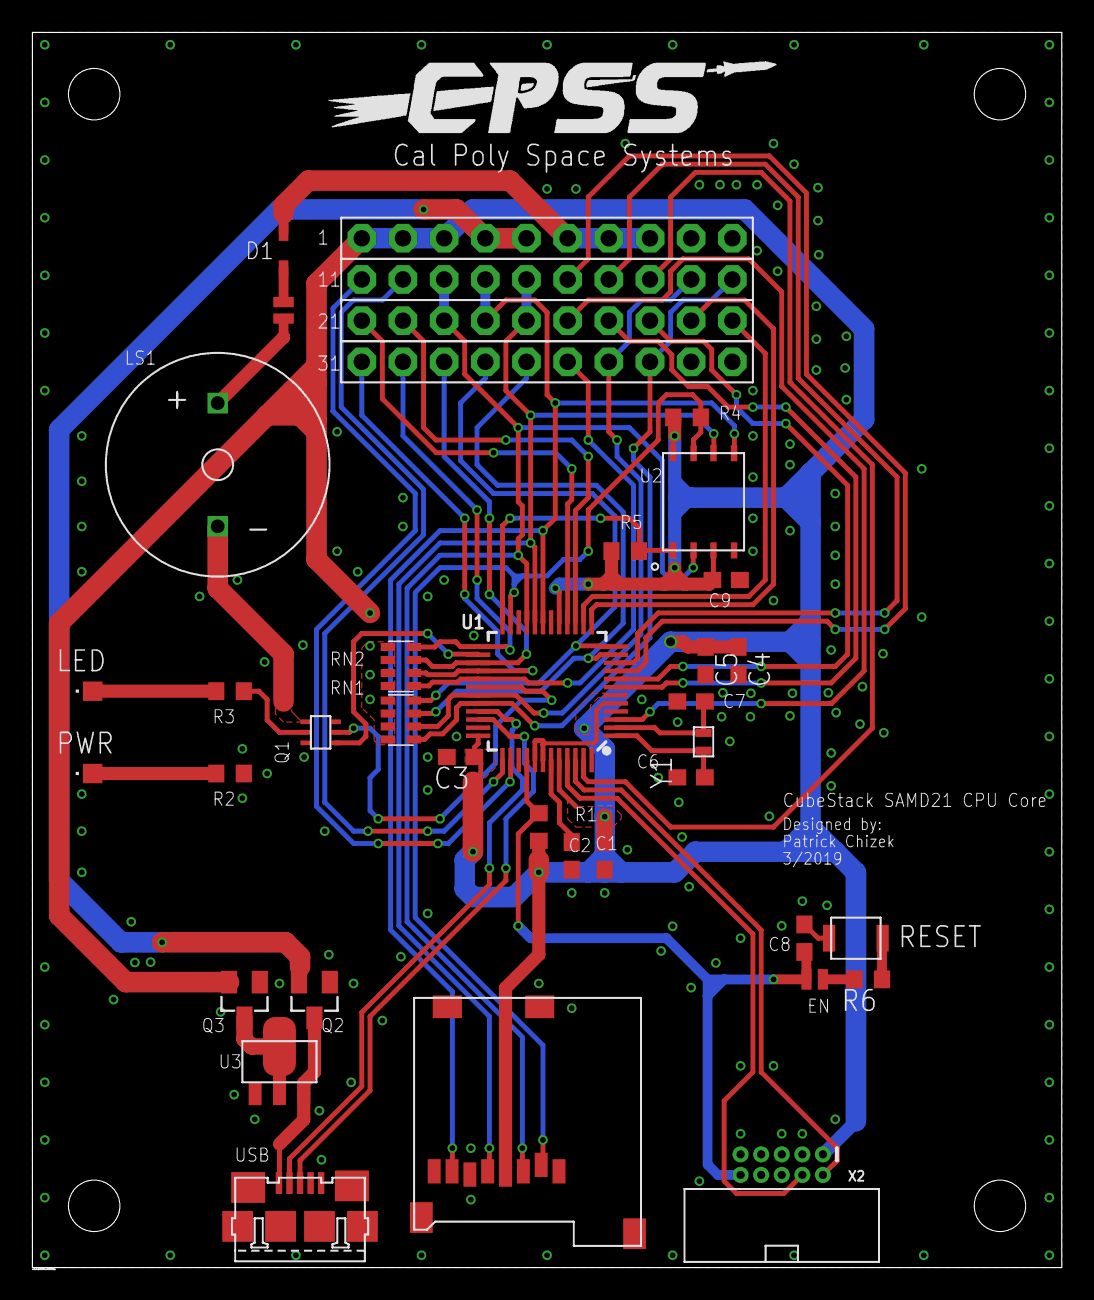
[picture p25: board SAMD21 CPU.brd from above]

Board: 2 copper layers, 63.5 x 76.2 mm, 38 parts (0 on the bottom side), 49 nets.

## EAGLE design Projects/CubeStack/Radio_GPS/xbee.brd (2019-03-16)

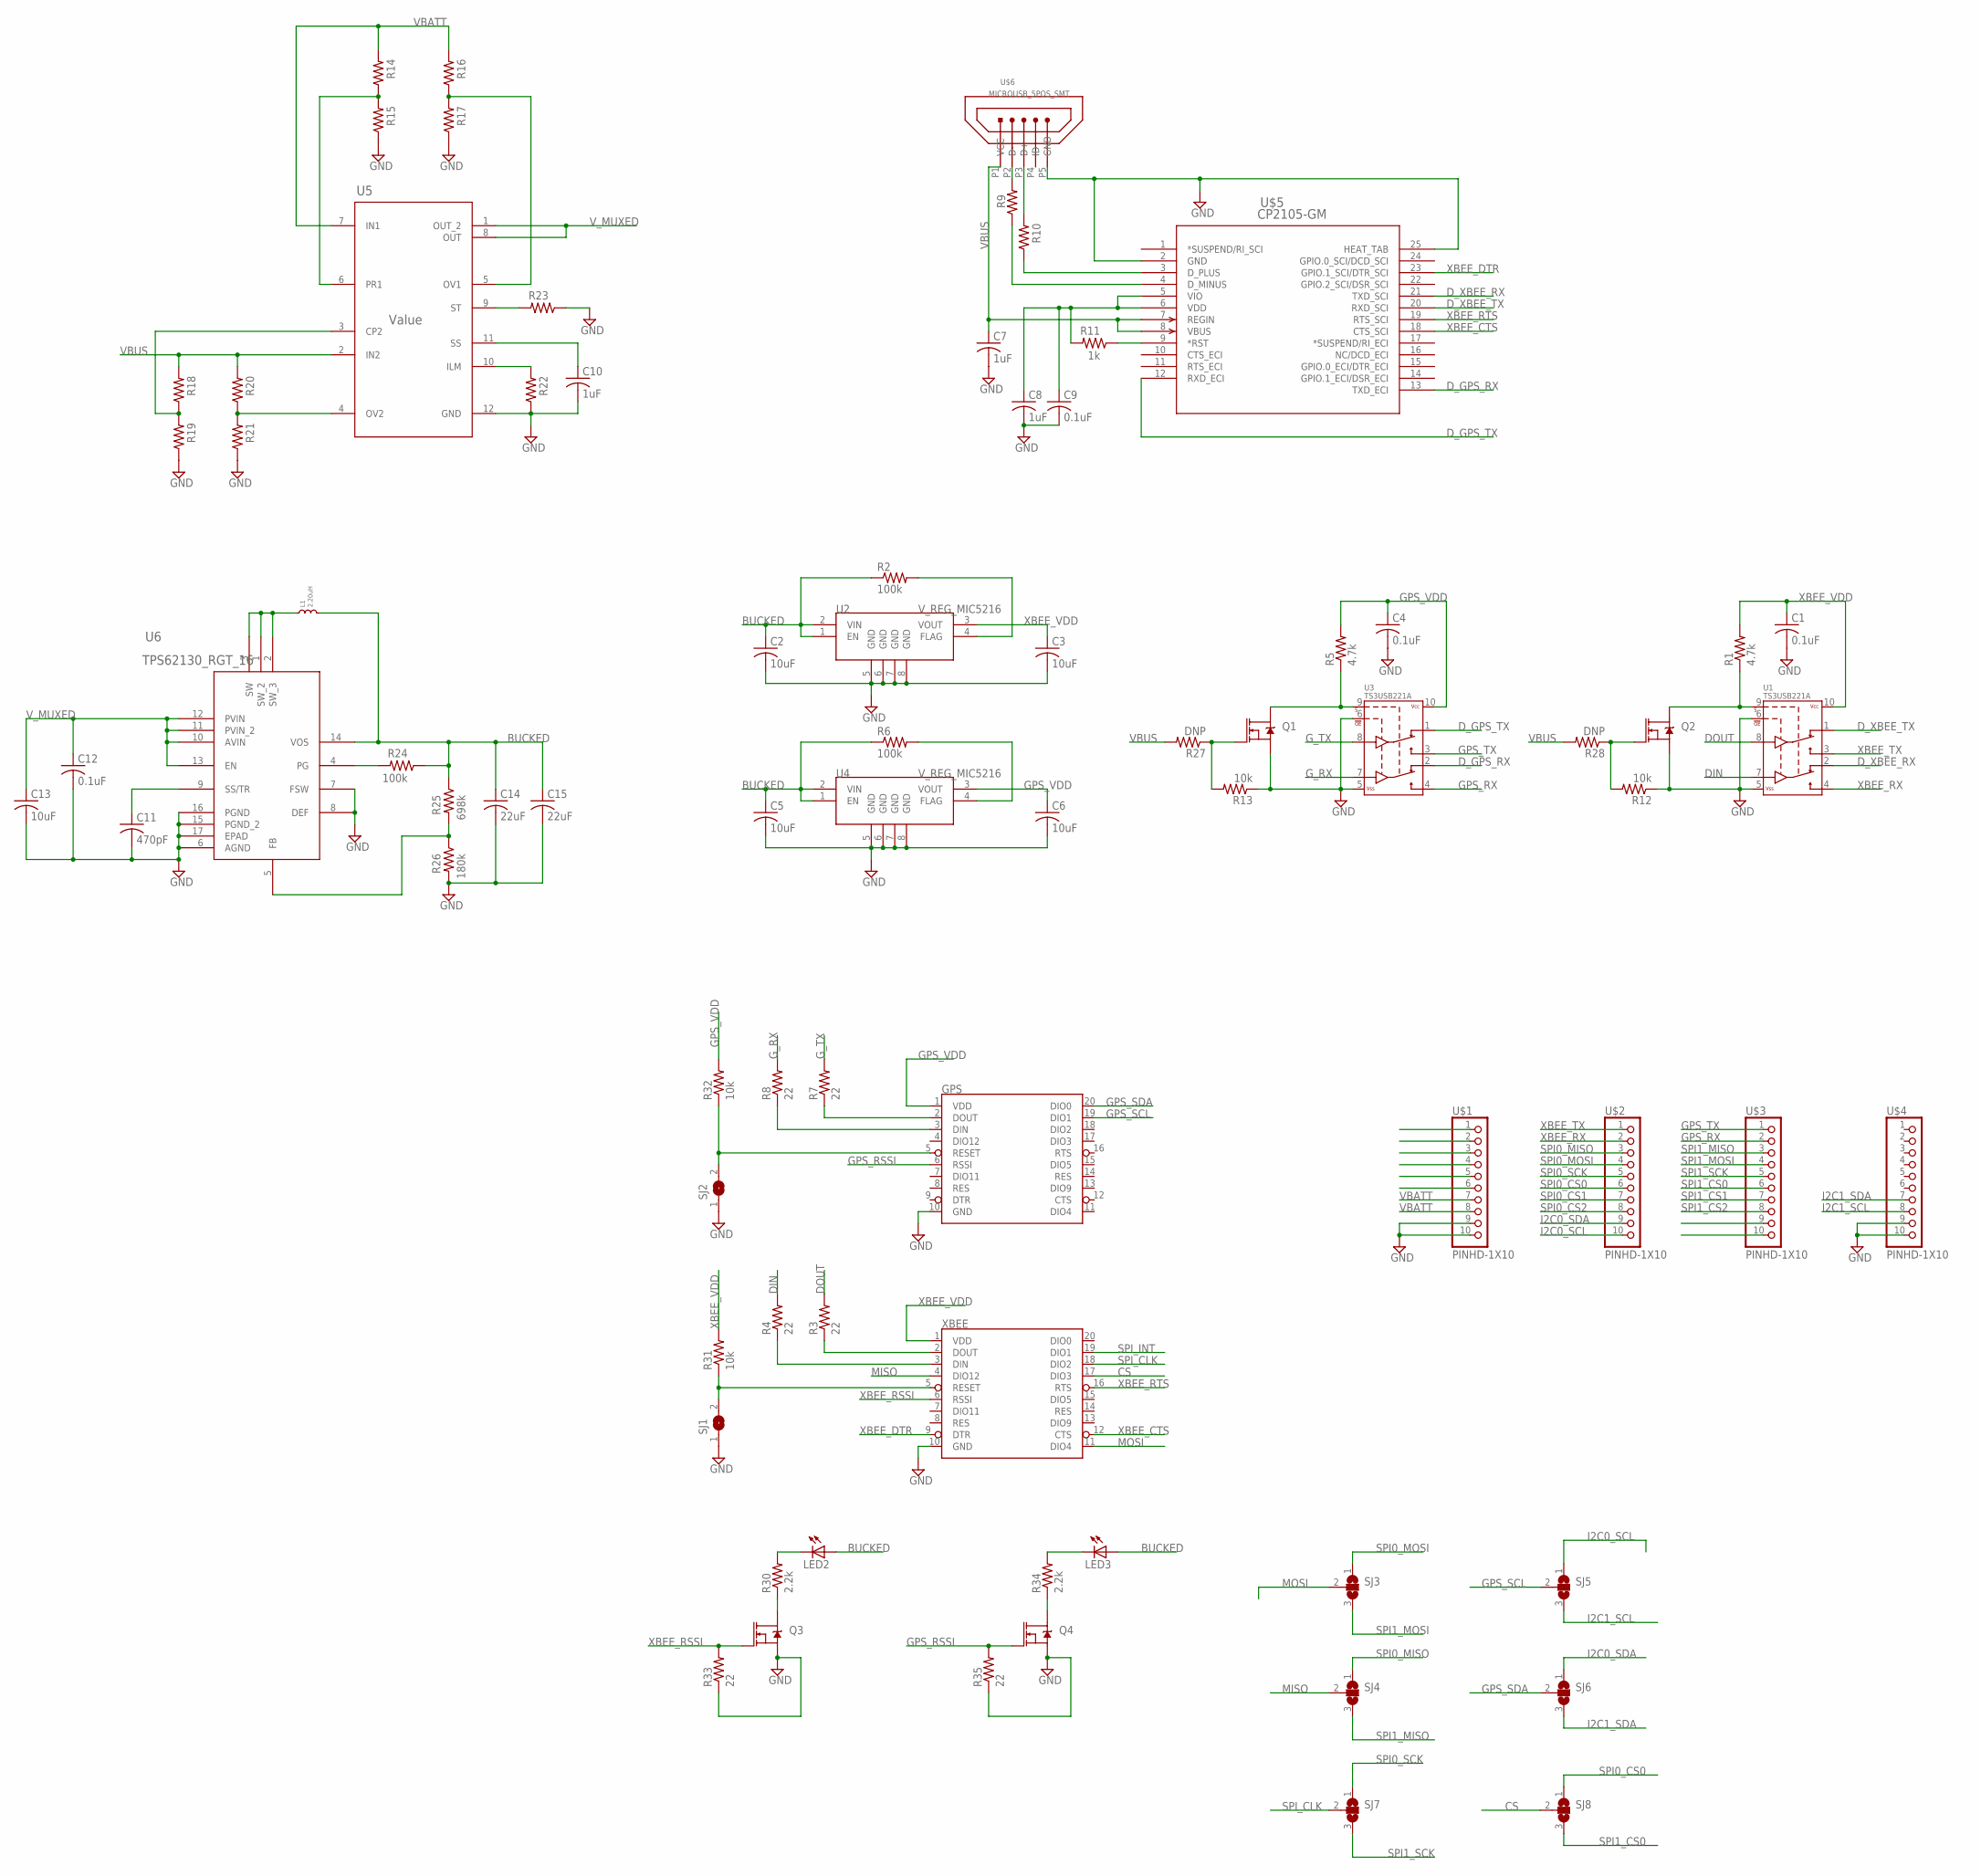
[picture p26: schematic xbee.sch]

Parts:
C1, C4, C9: 0.1uF; C0402
C2, C3, C5, C6, C13: 10uF; C1206
C7, C8, C10: 1uF; C0402
C11: 470pF; C0402
C12: 0.1uF; C0603
C14, C15: 22uF; C1210
GPS: XBEESMD; XBEE-SMD
L1: 2.20uH; XAL4020
LED2, LED3: LEDSML0603; SML0603
Q1, Q2, Q3, Q4: 310mA/60V/1.6Ω; SOT323
R1, R5: 4.7k; R0402
R2, R6, R24: 100k; R0402
R3, R4, R7, R8, R33, R35: 22; R0402
R9, R10, R14, R15, R16, R17, R18, R19, R20, R21, R22, R23: R-US_R0402; R0402
R11: 1k; R0402
R12, R13, R31, R32: 10k; R0402
R25: 698k; R0402
R26: 180k; R0402
R27, R28: DNP; R0402
R30, R34: 2.2k; R0402
SJ1, SJ2: SJW
SJ3, SJ4, SJ5, SJ6, SJ7, SJ8: SJ2W; SJ_2
U1, U3: TS3USB221A; QFN-10-RSE
U2, U4: V_REG_MIC5216; MSOP8
U5: Value; RUX0012A
U6: TPS62130_RGT_16; RGT16_1P7X1P7
U$1, U$2, U$3, U$4: PINHD-1X10; 1X10-BIG
U$5: CP2105-GM; QFN24_4X4
U$6: MICROUSB_5POS_SMT; RECPT_SMT_R/A
XBEE: XBEESMD; XBEE-SMD

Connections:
BUCKED: C2.1, C5.1, C14.1, C15.1, L1.2, LED2.A, LED3.A, R2.1, R6.1, R24.1, R25.1, U2.1 (EN), U2.2 (VIN), U4.1 (EN), U4.2 (VIN), U6.14 (VOS)
CS: SJ8.2, XBEE.17 (DIO3)
DIN: R4.2, U1.7 (D-)
DOUT: R3.2, U1.8 (D+)
D_GPS_RX: U3.2 (1D-), U$5.13 (TXD_ECI)
D_GPS_TX: U3.1 (1D+), U$5.12 (RXD_ECI)
D_XBEE_RX: U1.2 (1D-), U$5.21 (TXD_SCI)
D_XBEE_TX: U1.1 (1D+), U$5.20 (RXD_SCI)
GND: C1.2, C2.2, C3.2, C4.2, C5.2, C6.2, C7.2, C8.2, C9.2, C10.2, C11.2, C12.2, C13.2, C14.2, C15.2, GPS.10 (GND), Q1.2 (S), Q2.2 (S), Q3.2 (S), Q4.2 (S), R12.1, R13.1, R15.1, R17.1, R19.1, R21.1, R22.1, R23.1, R26.2, R33.1, R35.1, SJ1.1, SJ2.1, U1.5 (VSS), U1.6 (!OE), U2.5 (GND), U2.6 (GND), U2.7 (GND), U2.8 (GND), U3.5 (VSS), U3.6 (!OE), U4.5 (GND), U4.6 (GND), U4.7 (GND), U4.8 (GND), U5.12 (GND), U6.6 (AGND), U6.7 (FSW), U6.8 (DEF), U6.15 (PGND_2), U6.16 (PGND), U6.17 (EPAD), U$1.9, U$1.10, U$4.9, U$4.10, U$5.2 (GND), U$5.25 (HEAT_TAB), U$6.P5 (GND), XBEE.10 (GND)
GPS_RSSI: GPS.6 (RSSI), Q4.1 (G), R35.2
GPS_RX: U3.4 (2D-), U$3.2
GPS_SCL: GPS.19 (DIO1), SJ5.2
GPS_SDA: GPS.20 (DIO0), SJ6.2
GPS_TX: U3.3 (2D+), U$3.1
GPS_VDD: C4.1, C6.1, GPS.1 (VDD), R5.2, R32.2, U3.10 (VCC), U4.3 (VOUT)
G_RX: R8.2, U3.7 (D-)
G_TX: R7.2, U3.8 (D+)
I2C0_SCL: SJ5.1, U$2.10
I2C0_SDA: SJ6.1, U$2.9
I2C1_SCL: SJ5.3, U$4.8
I2C1_SDA: SJ6.3, U$4.7
MISO: SJ4.2, XBEE.4 (DIO12)
MOSI: SJ3.2, XBEE.11 (DIO4)
unnamed: R2.2, U2.4 (FLAG)
unnamed: R3.1, XBEE.2 (DOUT)
unnamed: R4.1, XBEE.3 (DIN)
unnamed: R6.2, U4.4 (FLAG)
unnamed: GPS.2 (DOUT), R7.1
unnamed: GPS.3 (DIN), R8.1
unnamed: R9.2, U$6.P2 (D-)
unnamed: R10.2, U$6.P3 (D+)
unnamed: R10.1, U$5.3 (D_PLUS)
unnamed: R9.1, U$5.4 (D_MINUS)
unnamed: R22.2, U5.10 (ILM)
unnamed: C8.1, C9.1, R11.2, U$5.5 (VIO), U$5.6 (VDD)
unnamed: Q1.3 (D), R5.1, U3.9 (S)
unnamed: Q2.3 (D), R1.1, U1.9 (S)
unnamed: R11.1, U$5.9 (*RST)
unnamed: R14.1, R15.2, U5.6 (PR1)
unnamed: R16.1, R17.2, U5.5 (OV1)
unnamed: R18.1, R19.2, U5.3 (CP2)
unnamed: R20.1, R21.2, U5.4 (OV2)
unnamed: C11.1, U6.9 (SS/TR)
unnamed: C10.1, U5.11 (SS)
unnamed: Q1.1 (G), R13.2, R27.1
unnamed: R23.2, U5.9 (ST)
unnamed: R25.2, R26.1, U6.5 (FB)
unnamed: Q2.1 (G), R12.2, R28.1
unnamed: R24.2, U6.4 (PG)
unnamed: L1.1, U6.1 (SW_2), U6.2 (SW_3), U6.3 (SW)
unnamed: LED2.C, R30.2
unnamed: Q3.3 (D), R30.1
unnamed: Q4.3 (D), R34.1
unnamed: LED3.C, R34.2
unnamed: R31.1, SJ1.2, XBEE.5 (RESET)
unnamed: GPS.5 (RESET), R32.1, SJ2.2
SPI0_CS0: SJ8.1, U$2.6
SPI0_CS1: U$2.7
SPI0_CS2: U$2.8
SPI0_MISO: SJ4.1, U$2.3
SPI0_MOSI: SJ3.1, U$2.4
SPI0_SCK: SJ7.1, U$2.5
SPI1_CS0: SJ8.3, U$3.6
SPI1_CS1: U$3.7
SPI1_CS2: U$3.8
SPI1_MISO: SJ4.3, U$3.3
SPI1_MOSI: SJ3.3, U$3.4
SPI1_SCK: SJ7.3, U$3.5
SPI_CLK: SJ7.2, XBEE.18 (DIO2)
SPI_INT: XBEE.19 (DIO1)
VBATT: R14.2, R16.2, U5.7 (IN1), U$1.7, U$1.8
VBUS: C7.1, R18.2, R20.2, R27.2, R28.2, U5.2 (IN2), U$5.7 (REGIN), U$5.8 (VBUS), U$6.P1 (VCC)
V_MUXED: C12.1, C13.1, U5.1 (OUT_2), U5.8 (OUT), U6.10 (AVIN), U6.11 (PVIN_2), U6.12 (PVIN), U6.13 (EN)
XBEE_CTS: U$5.18 (CTS_SCI), XBEE.12 (CTS)
XBEE_DTR: U$5.23 (GPIO.1_SCI/DTR_SCI), XBEE.9 (DTR)
XBEE_RSSI: Q3.1 (G), R33.2, XBEE.6 (RSSI)
XBEE_RTS: U$5.19 (RTS_SCI), XBEE.16 (RTS)
XBEE_RX: U1.4 (2D-), U$2.2
XBEE_TX: U1.3 (2D+), U$2.1
XBEE_VDD: C1.1, C3.1, R1.2, R31.2, U1.10 (VCC), U2.3 (VOUT), XBEE.1 (VDD)

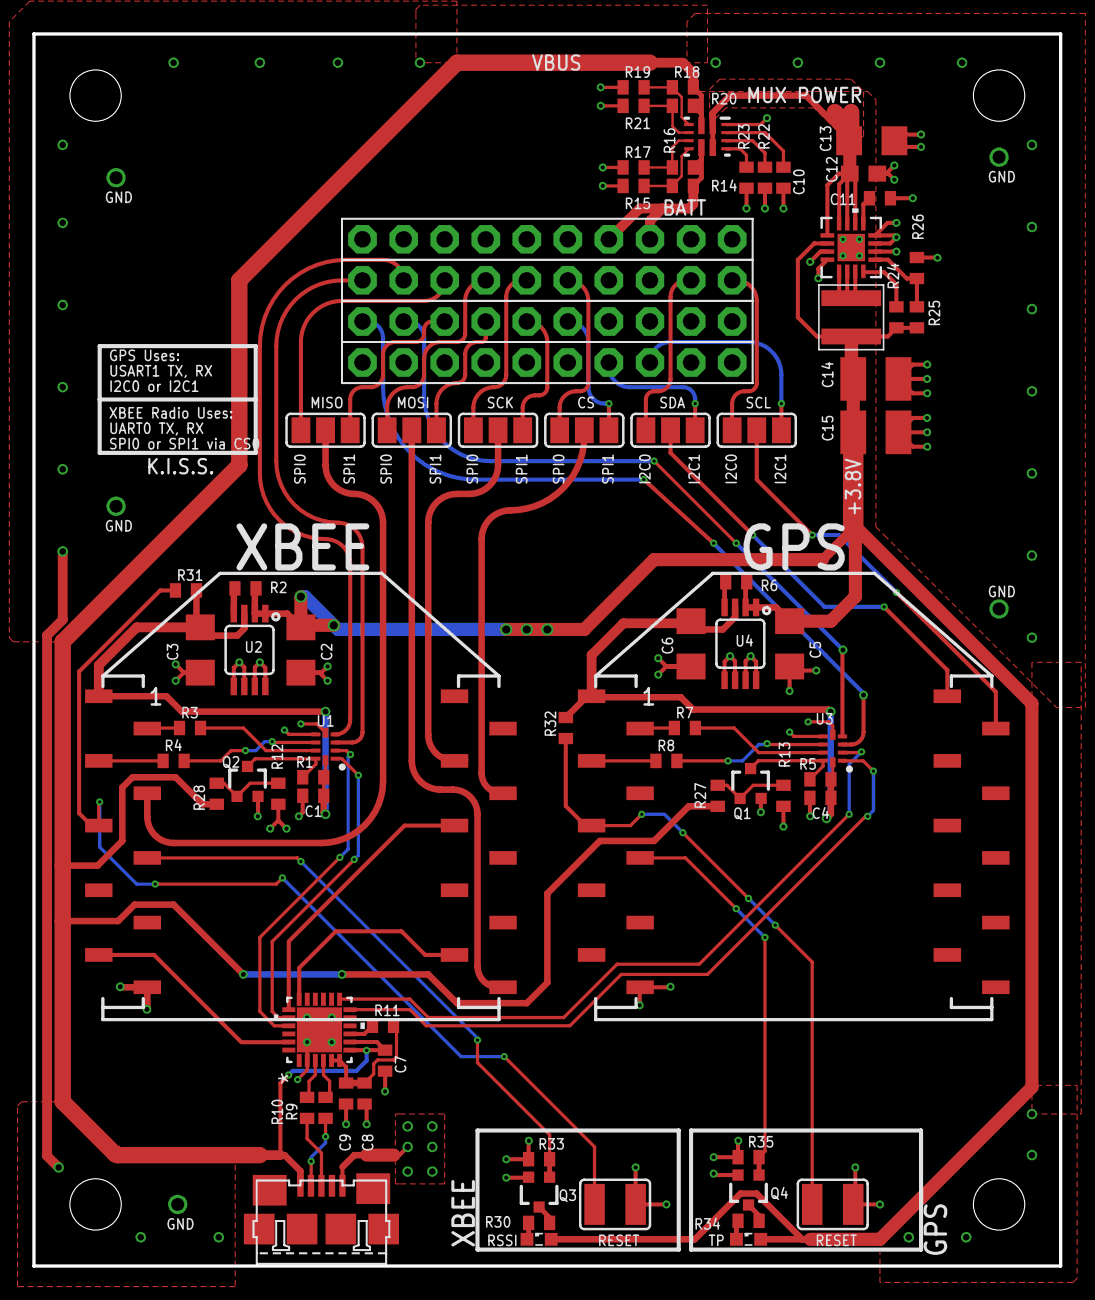
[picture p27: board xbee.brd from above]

Board: 2 copper layers, 63.5 x 76.2 mm, 78 parts (0 on the bottom side), 75 nets.

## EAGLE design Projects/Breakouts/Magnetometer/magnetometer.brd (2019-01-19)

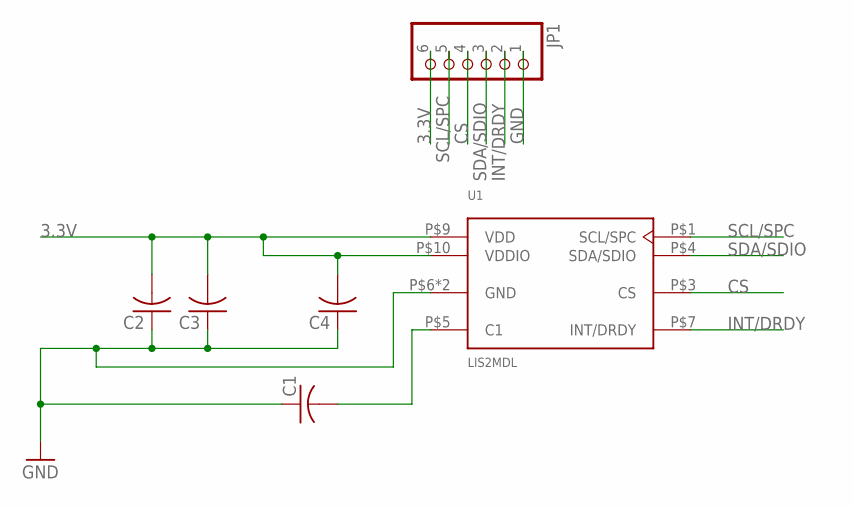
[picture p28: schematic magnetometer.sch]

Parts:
C1, C2, C3, C4: C-USC0805; C0805
JP1: PINHD-1X6; 1X06
U1: LIS2MDL; LGA-12

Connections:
3.3V: C2.2, C3.2, C4.2, JP1.6, U1.P$9 (VDD), U1.P$10 (VDDIO)
C1: C1.2, U1.P$5 (C1)
CS: JP1.4, U1.P$3 (CS)
GND: C1.1, C2.1, C3.1, C4.1, JP1.1, U1.P$6 (GND), U1.P$8 (GND)
INT/DRDY: JP1.2, U1.P$7 (INT/DRDY)
SCL/SPC: JP1.5, U1.P$1 (SCL/SPC)
SDA/SDIO: JP1.3, U1.P$4 (SDA/SDIO)


Board: 2 copper layers, 14.4 x 17.9 mm, 6 parts (0 on the bottom side), 7 nets.

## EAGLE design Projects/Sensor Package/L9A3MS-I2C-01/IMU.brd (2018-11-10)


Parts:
A3G4250D: A3G4250D; LGA-16
C1, C2, C5, C6, C9: 100 nF; C0603
C3, C10: 10 uF; C0603
C4, C7: 10 nF; C0603
C8: 470 nF; C0603
MS5611: MS5611-01BA03
R1: 10 kOhm; R0603
U$1: DF12-20PIN_CONNECTOR_RECEPT; DF12-RECEPT
U$2: LSM9DS1LONG_PAD; LGA

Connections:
3.3V: A3G4250D.P1 (VDDIO), A3G4250D.P16 (VDD), C2.2, C3.2, C5.2, C6.1, C9.1, C10.1, MS5611.1 (VDD), MS5611.2 (PS), U$1.P$1, U$2.P1 (VDDIO), U$2.P3 (VDDIO), U$2.P7 (CS_A/G), U$2.P8 (CS_M), U$2.P22 (VDD), U$2.P23 (VDD)
12V: U$1.P$2, U$1.P$3
AIN8: U$1.P$17
AIN9: U$1.P$18
AIN10: U$1.P$19
D46: U$1.P$11, U$2.P11 (INT1_A/G)
D47: A3G4250D.P7 (INT1), U$1.P$12
D48: U$1.P$13
D49: U$1.P$14
D50: U$1.P$15
D51: U$1.P$16
GND: A3G4250D.P8 (RES1), A3G4250D.P9 (RES2), A3G4250D.P10 (RES3), A3G4250D.P11 (RES4), A3G4250D.P12 (RES5), A3G4250D.P13 (GND), C1.1, C2.1, C3.1, C4.1, C5.1, C7.1, C8.1, C9.2, C10.2, MS5611.4 (CSB), MS5611.5 (CSB2), U$1.P$4, U$1.P$5, U$1.P$20, U$2.P5 (SDO_AG), U$2.P6 (SDO_M), U$2.P14 (RES), U$2.P15 (RES), U$2.P16 (RES), U$2.P17 (RES), U$2.P18 (RES), U$2.P19 (GND), U$2.P20 (GND)
MISO: U$1.P$6
MOSI: U$1.P$7
unnamed: A3G4250D.P14 (PLLFILT), C7.2, R1.1
unnamed: C8.2, R1.2
unnamed: C6.2, MS5611.3 (GND)
unnamed: C4.2, U$2.P21 (CAP)
unnamed: C1.2, U$2.P24 (C1)
SCK: U$1.P$8
SCL: A3G4250D.P2 (SCL/SCK), MS5611.8 (SCLK), U$1.P$10, U$2.P2 (SCL/SPC)
SDA: A3G4250D.P3 (SDA/SDI), MS5611.7 (SDI/SDA), U$1.P$9, U$2.P4 (SDA/SDI/SDO)


Board: 2 copper layers, 38.1 x 25.5 mm, 15 parts (0 on the bottom side), 12 nets.

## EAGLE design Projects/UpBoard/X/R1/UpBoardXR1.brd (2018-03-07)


Board: 2 copper layers, 88.9 x 76.2 mm, 75 parts (0 on the bottom side), 101 nets.

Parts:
C1: 10pF; C0603
C2, C3, C4, C5: 22pF; C0603
C6: 10n; C0603
C7: 100n; C0603
C8, C9, C10, C11, C12: 10uF; A/3216-18R
CN1, CN2, CN3, CN4: 100nF; 1206-4
D1, D2: SOD323
ERASE: 1000P; B3U-1000P
GND: LSP10
IC1: SAM3X8E(ARDUINO); 144-LEAD_LQFP
IC2: W25N01GVZEIG/IT; WSON
JP1: JTAG; 2X05
JP2: CONFIG; 2X03
JP3: 1X02
L1, L2, L3: C0402
LED1, LED2, LED3: CHIPLED_0805
LS1: AI-1440-TWT-24V-2-R; AI-1440-TWT-24-2-R
PS1-1:C1: 10nF; C0603
PS1-1:C2, PS1-1:C3: 100nF; C0603
PS1-1:C4: 1uF; C0805
PS1-1:C5: 4.7uF; C1206
PS1-1:C6: 4.7uF; C0805
PS1-1:C7, PS1-1:C8: 10uF; C1206
PS1-1:C9: 100uF; C0805
PS1-1:D1: S10M-TP; DO-214AB
PS1-1:IC1: TPS2115ADRB; SON-8
PS1-1:L1: LPS6225-103MRB; INDM600X600X240N
PS1-1:L2: Wurth 742792641; R0603
PS1-1:PS1: R-78E5.0-1.0
PS1-1:PS2: AZ1117C; SOT89
PS1-1:R1: 330; R0603
PWR: CHIPLED_0805
Q1, Q2: MBT3904DW2T1; SOT-363
R1, R2: 39; R0603
R3, R4: 220R; R0402
R5: 6.8K; R0603
R6: 0R; R0603
RESET: 1000P; B3U-1000P
RN1: 65R; CTS742C083
RN2, RN3: 4.7K; CTS742C083
RN4: 100K; CTS742C083
SD1: CONN_MICROSD
SJ1: SJ_2
SJ2, SJ3: SOLBRDG
X1, X2, X3, X4: 16POS_RIBBON; 2X08
XA1: DF12-20PIN_CONNECTOR_HEADER; DF12-HEADER
XP1: 2POSTERMINALBLOCK.25"PITCH; OSTYK22102030
XU1: MICROUSB_5POS_SMT; RECPT_SMT_R/A
Y1: FH1200001; MINISMD
Y2: ABS05; FC-12M

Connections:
1.8V: C12.+, CN1.P$1, CN1.P$2, CN3.P$1, CN3.P$2, CN3.P$3, CN3.P$4, IC1.P$10, IC1.P$45, IC1.P$56, IC1.P$61, IC1.P$104, IC1.P$124, L1.1
3.3V: C6.1, C7.2, C8.+, CN1.P$3, CN1.P$4, CN4.P$1, CN4.P$2, CN4.P$3, CN4.P$4, IC1.P$11, IC1.P$52, IC1.P$57, IC1.P$62, IC1.P$105, IC1.P$125, IC2.P8, JP1.1, L2.1, L3.1, LED1.A, LED2.A, LED3.A, PS1-1:PS2.2, PS1-1:PS2.2@1, PWR.A, R4.2, RN2.5, RN2.6, RN2.7, RN2.8, RN4.5, RN4.6, RN4.7, RN4.8, SD1.4, SJ3.P$2, X1.1, X2.1, X3.1, X4.1, XA1.P$1, XA1.P$2
5V: D2.2, JP2.2, PS1-1:C3.1, PS1-1:C4.1, PS1-1:C9.1, PS1-1:IC1.7, PS1-1:PS2.3
A0: IC1.P$78, X3.15
A1: IC1.P$79, X3.16
A2: IC1.P$80, X4.15
A3: IC1.P$81, X4.16
A4: IC1.P$82, XA1.P$17
A5: IC1.P$83, XA1.P$18
A6: IC1.P$84, XA1.P$19
A7: IC1.P$85, X1.15
A8: IC1.P$88, X1.16
A9: IC1.P$89, X2.15
A10: IC1.P$90, X2.16
AREF: SJ1.3, X1.14, X2.14, X3.14, X4.14
AREF0/D51: SJ1.2, XA1.P$16
D2: IC1.P$144, X2.13
D3: IC1.P$139, X1.11
D4: IC1.P$137, X1.12
D5: IC1.P$136, X1.13
D6: IC1.P$135, IC2.P7
D7: IC1.P$134, IC2.P1, JP3.1, R4.1
D8: IC1.P$133, IC2.P3, JP3.2
D9: IC1.P$132, RN3.1
D10: IC1.P$102, SD1.2
D11: IC1.P$20, RN3.2
D12: IC1.P$21, RN3.3
D13: IC1.P$68, RN3.4
D37: IC1.P$63, X3.11
D38: IC1.P$64, X3.12
D39: IC1.P$65, X3.13
D40: IC1.P$66, X4.11
D41: IC1.P$67, X4.12
D42: IC1.P$71, X4.13
D46: IC1.P$99, XA1.P$11
D47: IC1.P$98, XA1.P$12
D48: IC1.P$97, XA1.P$13
D49: IC1.P$96, XA1.P$14
D50: IC1.P$95, XA1.P$15
D51: IC1.P$94, SJ1.1
D+: IC1.P$37, R1.1, XU1.P3
D-: IC1.P$38, R2.1, XU1.P2
ERASE: ERASE.P$2, IC1.P$130, JP2.4
GND: C1.2, C2.2, C3.2, C4.1, C5.1, C7.1, C8.-, C9.-, C10.-, C11.-, C12.-, CN1.P$5, CN1.P$6, CN1.P$7, CN1.P$8, CN2.P$2, CN2.P$3, CN2.P$4, CN3.P$5, CN3.P$6, CN3.P$7, CN3.P$8, CN4.P$5, CN4.P$6, CN4.P$7, CN4.P$8, GND.MP, IC1.P$12, IC1.P$33, IC1.P$44, IC1.P$54, IC1.P$58, IC1.P$74, IC1.P$106, IC1.P$126, IC2.P4, IC2.TH, JP1.3, JP1.5, JP1.9, JP2.6, PS1-1:C1.2, PS1-1:C2.2, PS1-1:C3.2, PS1-1:C4.2, PS1-1:C5.2, PS1-1:C6.2, PS1-1:C7.2, PS1-1:C8.2, PS1-1:C9.2, PS1-1:IC1.3, PS1-1:IC1.5, PS1-1:IC1.PAD, PS1-1:PS1.2, PS1-1:PS2.1, PS1-1:R1.2, Q1.P$1, Q1.P$4, Q2.P$1, Q2.P$4, R3.2, R5.1, RN1.8, SD1.6, SD1.GND1, SD1.GND2, SD1.GND3, SJ2.P$2, X1.2, X2.2, X3.2, X4.2, XA1.P$4, XA1.P$5, XA1.P$20, XP1.P$2, XU1.P5, Y1.GND2, Y1.GND4
HV: D1.2, PS1-1:C7.1, PS1-1:D1.-, PS1-1:L1.1, X1.3, X2.3, X3.3, X4.3
JTAG_SEL: IC1.P$46, R3.1
JTAG_TCK: IC1.P$28, JP1.4, RN4.2
JTAG_TDI: IC1.P$29, JP1.8, RN4.3
JTAG_TDO: IC1.P$30, JP1.6
JTAG_TMS: IC1.P$31, JP1.2, RN4.1
LS_DRIVE: D1.1, D2.1, R6.2
MISO: IC1.P$108, IC2.P2, SD1.7, X1.6, X2.6, X3.6, X4.6, XA1.P$6
MOSI: IC1.P$109, IC2.P5, SD1.3, X1.7, X2.7, X3.7, X4.7, XA1.P$7
M_RESET: C6.2, IC1.P$47, JP1.10, JP2.5, RESET.P$2, RN4.4
unnamed: LED3.C, RN1.2
unnamed: IC1.P$42, R1.2
unnamed: LED2.C, RN1.3
unnamed: PS1-1:D1.+, XP1.P$1
unnamed: PWR.C, RN1.1
unnamed: RESET.P$1, SJ2.P$1
unnamed: LED1.C, RN1.4
unnamed: Q2.P$5, RN3.5
unnamed: IC1.P$43, R2.2
unnamed: Q2.P$3, RN1.7
unnamed: Q1.P$6, RN1.6
unnamed: Q1.P$3, RN1.5
unnamed: Q1.P$2, RN3.6
unnamed: Q1.P$5, RN3.7
unnamed: Q2.P$2, RN3.8
unnamed: ERASE.P$1, SJ3.P$1
unnamed: C5.2, IC1.P$35, Y1.P3
unnamed: LS1.-, Q2.P$6
unnamed: C4.2, IC1.P$36, Y1.P1
unnamed: C2.1, IC1.P$49, Y2.2
unnamed: C3.1, IC1.P$48, Y2.1
unnamed: LS1.+, R6.1
unnamed: C1.1, IC1.P$40, R5.2
PS1-1:BATT_5V: PS1-1:C8.1, PS1-1:IC1.8, PS1-1:PS1.3
PS1-1:N$2: PS1-1:C5.1, PS1-1:L1.2, PS1-1:PS1.1
PS1-1:N$3: PS1-1:IC1.4, PS1-1:R1.1
PS1-1:USB_FILTERED: PS1-1:C2.1, PS1-1:C6.1, PS1-1:IC1.6, PS1-1:L2.2
RX/D0: IC1.P$27, JP2.1, X2.11
RXS0: IC1.P$3, X2.4
RXS1: IC1.P$5, X3.4
RXS2: IC1.P$107, X1.4
RXS3: IC1.P$18, X4.4
SCK: IC1.P$110, IC2.P6, SD1.5, X1.8, X2.8, X3.8, X4.8, XA1.P$8
SCL: IC1.P$87, RN2.1, X1.10, X2.10, X3.10, X4.10, XA1.P$10
SCL1: IC1.P$70, RN2.3
SDA: IC1.P$86, RN2.2, X1.9, X2.9, X3.9, X4.9, XA1.P$9
SDA1: IC1.P$9, RN2.4
TX/D1: IC1.P$2, JP2.3, X2.12
TXS0: IC1.P$4, X2.5
TXS1: IC1.P$6, X3.5
TXS2: IC1.P$72, X1.5
TXS3: IC1.P$17, X4.5
UOTGID: IC1.P$129, XU1.P4
VBUS: PS1-1:C1.1, PS1-1:L2.1, XU1.P1
VDDANA: C10.+, CN2.P$7, IC1.P$73, L2.2
VDDPLL: C11.+, CN2.P$6, IC1.P$34, L1.2
VDDUTMI: C9.+, CN2.P$8, IC1.P$41, L3.2

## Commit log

2017-09-24 Committed Josh's IMU to Repository
    [IMU.brd, IMU.sch]
2017-09-24 Added Patch Circles to highlight areas to be revised
    [UpBoardX.sch]
2017-09-29 Revised overly complicated power system
    [UpBoardX.brd, UpBoardX.sch]
2017-10-10 Simplified power system
    [UpBoardX.brd, UpBoardX.sch]
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2017-10-12 Added CAM file section for UBX
    [UpBoardX.drills.xln]
2017-10-12 Finished labeling, removed SPI pull ups
    [UpBoardX.brd, UpBoardX.sch]
2017-10-12 Fixed Labelling
    [IMU.brd, IMU.sch]
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2017-10-21 Initial Commit of the Radio Board
    Radio board PCB and schematic of Rev 1. Datasheets and BOM still to be added.
    [Radio_Board_R1.brd, Radio_Board_R1.sch]
2017-10-22 Added BOM and PCB GND connections for crystal
    [Radio_Board_R1.brd, Radio_Board_R1.sch, Radio_Board_R1_BOM.xlsx]
2017-10-25 Final Update of Radio Board
    Modified existing silkscreen with name and description on board.
    [Radio_Board_R1.brd]
2017-10-26 Add strain gauge board files
    Schematic and most of layout
    [EDI2CAP.CFG, STRAIN GAUGE BOARD.DSN, StrainGaugeBoard_R0_X0.brd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]
2017-10-30 First fixes, schematic appearance changes
    Connected D+ line on native USB port. Added title block and reorganized
    schematic to fit on a size C sheet. Revision number is now 1.
    [UpBoardX.brd, UpBoardX.sch]
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2017-10-31 Organized power supply into own module
    [UpBoardX.brd, UpBoardX.sch]
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2018-01-30 Added I2C data line
    [NanoRek.sch]
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2018-02-10 Revert "Added I2C data line"
    This reverts commit ce24847924fb5b1688f37034ce33982163fc9d56.
    [NanoRek.sch]
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2018-02-11 Added frame, replaced ATMEGA328P part
    [MicroRek.brd, MicroRek.sch]
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2018-02-24 Connected Flash corrctly, changed sheet size
    [UpBoardXR1.brd, UpBoardXR1.sch]
2018-02-26 Finished routing traces, front silkscreen.
    [UpBoardXR1.brd, UpBoardXR1.sch]
2018-02-27 Fixed refdes
    [UpBoardXR1.brd, UpBoardXR1.sch]
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2018-02-28 Added in and routed bjt arrays
    [UpBoardXR1.brd, UpBoardXR1.sch]
2018-02-28 Fixed naming and silkscreen
    [UpBoardXR1.brd, UpBoardXR1.sch]
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2018-03-07 created and finished upboard radio adapter
    [UpBoard-Radio.brd]
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2018-04-02 Updated MicroRek Board Layout
    [MicroRek.brd]
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2018-04-07 LOTS of work on board layout
    [MicroRek.brd, MicroRek.sch]
2018-04-09 Added CAM Files for UBXR1 and Adapters
    [UpBoardXR1_BOM.csv, UpBoardXR1_BOM.xlsx]
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2018-04-21 MicroRek Updates
    Changed inductor package
    Fixed some wiring
    Fixed Crystal wiring (MAYBE)
    Will work more in the morning
    [MicroRek.brd, MicroRek.sch]
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2018-05-08 MicroRek Update
    Added pullup resistors and the mini icsp port
    [MicroRek.brd, MicroRek.sch]
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2018-05-16 small led nd pullup update
    [MicroRek.brd, MicroRek.sch]
2018-05-17 fixed pullup resistors
    [MicroRek.brd, MicroRek.sch]
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2018-05-19 started new board layout
    [MicroRek.brd]
2018-06-18 Oversized beacon PCB files
    Initial upload of KiCAD design file for a 222.25 to 223.29 MHz single tone transmitter. Uses the ADF4360-8 PLL and has an SPI breakout for control. All parts oversized to 0805 or larger for newbies t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
    [beacon_pll-B.Cu.gbr, beacon_pll-B.Mask.gbr, beacon_pll-B.Paste.gbr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]
2018-06-19 Mini Rek Upload
    Like the micro rek but with onboard transmitter. It's a little larger though
    [Lupo_Testing-B.Cu.gbr, Lupo_Testing-B.Mask.gbr, Lupo_Testing-B.Paste.gbr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]
2018-06-19 Basic power regulation schematic
    [CPSS_Power_Board.kicad_pcb, CPSS_Power_Board.sch]
2018-06-19 Added PDF outputs and cleaned up schematic
    [beacon_pll.sch]
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2018-07-16 Added intial schematics for pressure board rev 2
    [Pressure_Sensor_V2.kicad_pcb, Pressure_Sensor_V2.sch]
2018-08-25 Basic BOM, no parts just footprints and quantities
    [beacon_pll.csv]
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2018-09-16 First Draft of SAM3X CPU Core
    [SAM3X Core Module.brd, SAM3X Core Module.sch]
2018-11-10 Modified Libraries, Worked on STM32F3 Core
    [IMU.brd, IMU.sch, SAM3X Core Module.brd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]
2018-11-10 Fixed CAD Directories
    [IMU.sch, SAM3X Core Feature Drawing.brd, SAM3X Core Feature Drawing.sch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]
2018-11-11 Routed PWM, GPIO lines
    [STM32F3 Discovery Core.brd, STM32F3 Discovery Core.sch]
2018-12-20 Removed Feature Drawing examples
    [SAM3X Core Feature Drawing.brd, SAM3X Core Feature Drawing.sch]
2018-12-20 Completed STM32 Core to be Reviewed
    [STM32F3 Discovery Core.brd, STM32F3 Discovery Core.sch]
2018-12-20 Schematic and Layout of Sensor Board
    TODO: Fix silkscreen and organize schematic.
    [SB2.brd, SB2.sch]
2018-12-20 Depricated old Due CPU Core design
    [SAM3X Core Module Dep.brd, SAM3X Core Module Dep.sch]
2018-12-20 Modified Existing SAM3X CPU for New Bus Pinout
    [SAM3X Core Module.sch]
2018-12-21 Added radio board and component libraries
    [xbee.brd, xbee.sch]
2018-12-22 Added Via Stitching to Perimeter + Bus Pin Numbers
    [STM32F3 Discovery Core.brd]
2018-12-22 Organized Silkscreen + Added Bus Pin Numbers
    [SB2.brd]
2019-01-02 Created Power Distribution Board with FET Array
    TODO: Change component names
    [PDU1.brd, PDU1.sch]
2019-01-02 Update component names
    TODO: Change Resistor/Capacitor names
    [STM32F3 Discovery Core.brd, STM32F3 Discovery Core.sch]
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2019-01-18 Reorganized CircuitCAD Repo
    Divided into two sections: dependencies and projects. See readmes in each directory for more info
    [CPSS_Power_Board.kicad_pcb, CPSS_Power_Board.sch, EDI2CAP.CFG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]
2019-01-19 Add files via upload
    This folder will contain breakout boards.
    [magnetometer.brd, magnetometer.sch]
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2019-01-27 Add files via upload
    This is the EAGLE schematic for the pressure sensor board.
    [Pressure_Sensor_V2_schem.sch]
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2019-02-16 Added updated radio GPS board
    [xbee2.brd, xbee2.sch]
2019-03-16 Added some part values
    [xbee.brd, xbee2.sch]
2019-03-19 Create SAMD21 CPU.brd
    Finished SAMD21 CPU Design
    [SAMD21 CPU.brd]
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2019-03-19 Added more vias to SAMD21 Core
    [SAMD21 CPU.brd]
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2020-01-11 Added PTAP circuit CAD
    [Pressure_Sensor_V2_schem.brd, Pressure_Sensor_V2_schem.sch]
2020-01-18 Upload of DVR-VTX and PDU2 files
    [DVR-VTX1.brd, DVR-VTX1.sch, PDU2.brd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]

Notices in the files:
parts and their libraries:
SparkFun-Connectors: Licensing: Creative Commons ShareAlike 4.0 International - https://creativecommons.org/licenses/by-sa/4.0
